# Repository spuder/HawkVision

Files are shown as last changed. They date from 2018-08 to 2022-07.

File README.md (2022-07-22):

# HawkVision

Adapter board that makes it easy to mount a TBS unify nano to the Hawk 5

[Available for purchase on etsy](https://www.etsy.com/listing/630369832/hawk-vision-vtx-realpit?ref=shop_home_active_1)



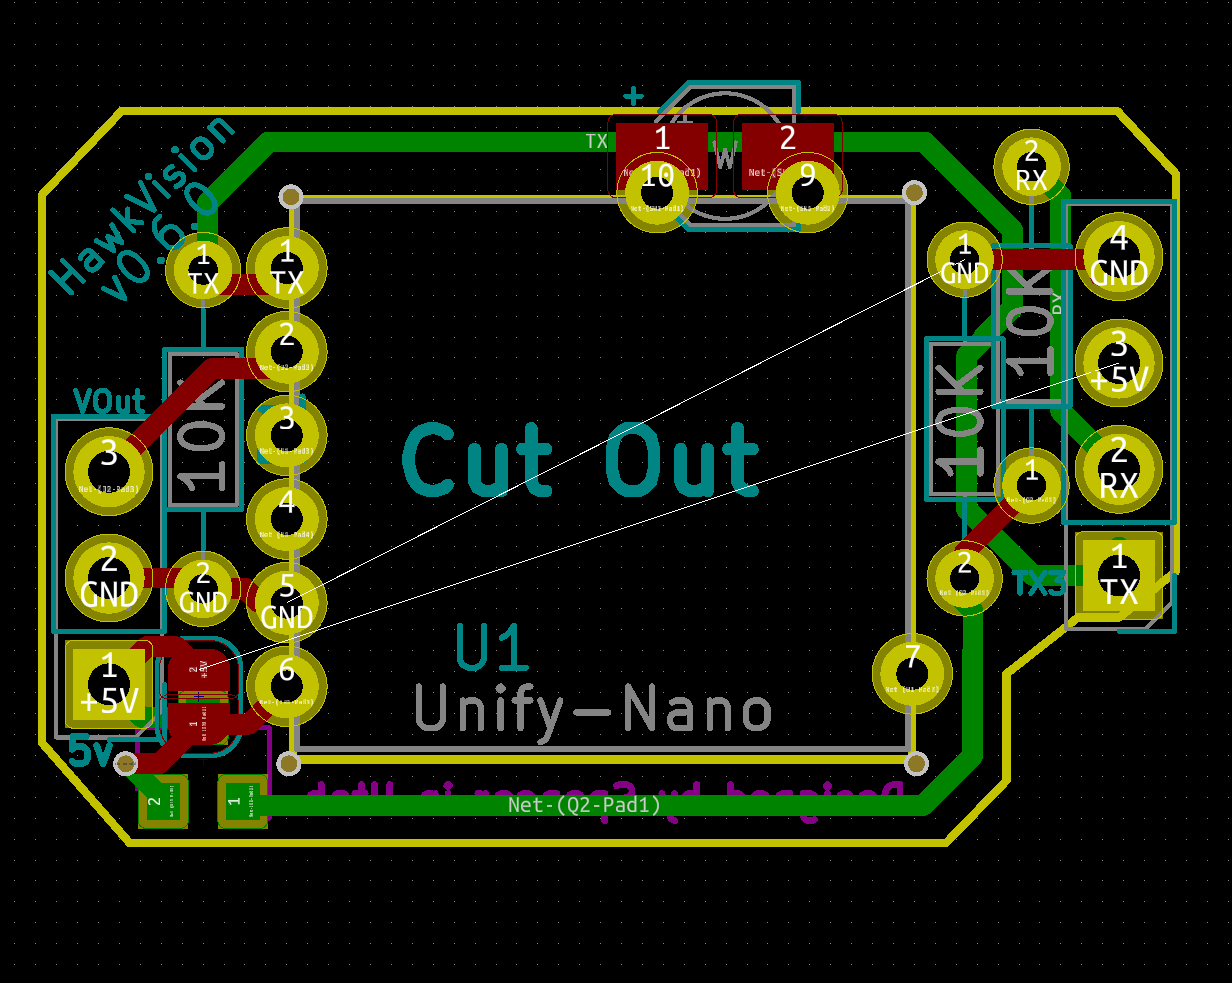
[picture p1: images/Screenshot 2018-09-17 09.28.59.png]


Based off the same idea as [whitenoise FPV](https://whitenoisefpv.com/collections/electronics/products/unify-nano-mounting-board) but designed specifically for the emax stack

## Schematic

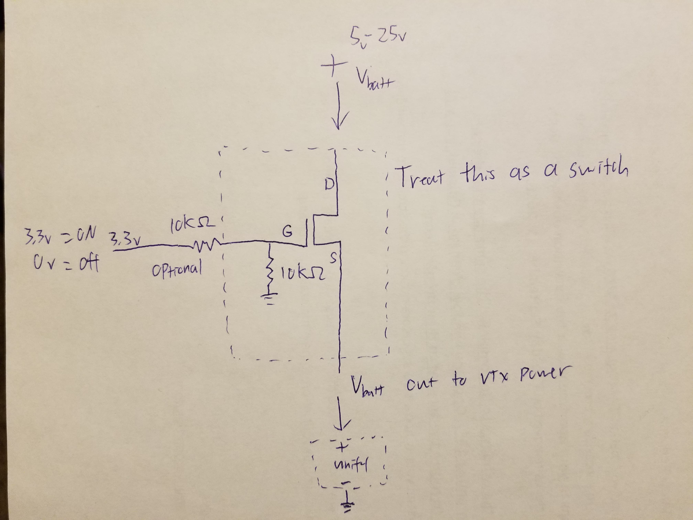
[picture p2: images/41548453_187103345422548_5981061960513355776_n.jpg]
  
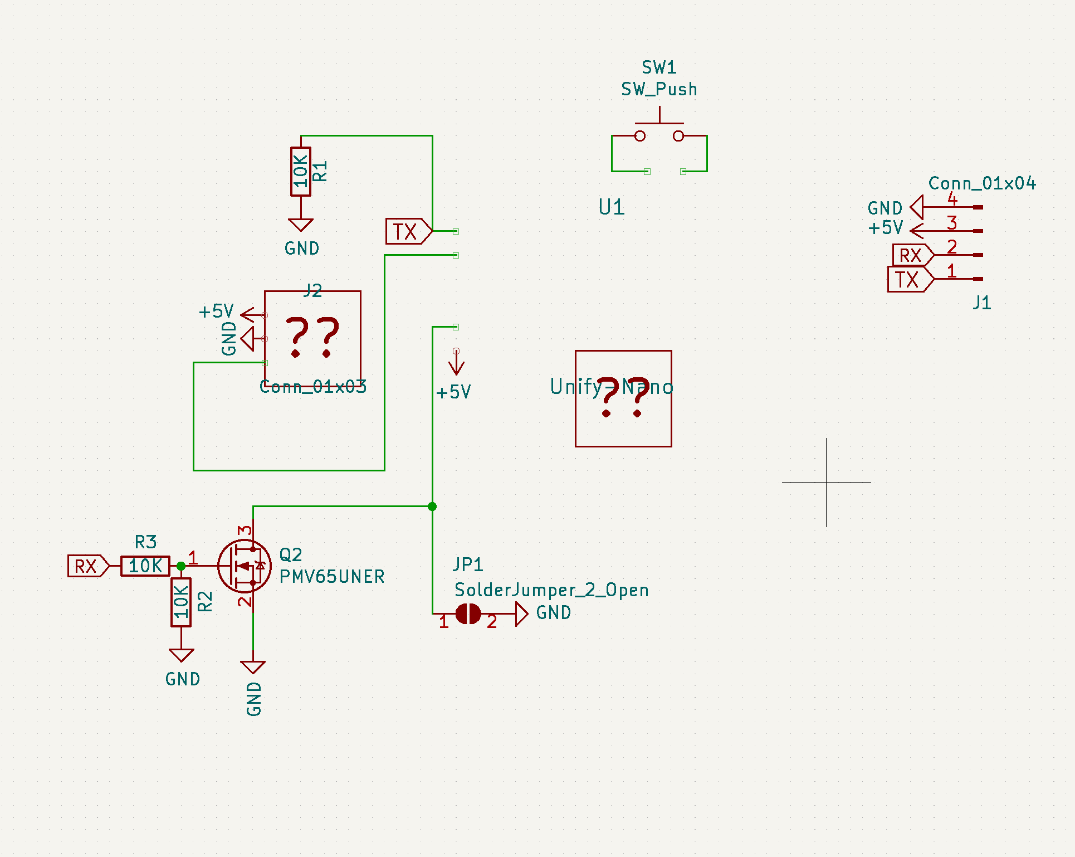
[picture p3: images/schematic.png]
  
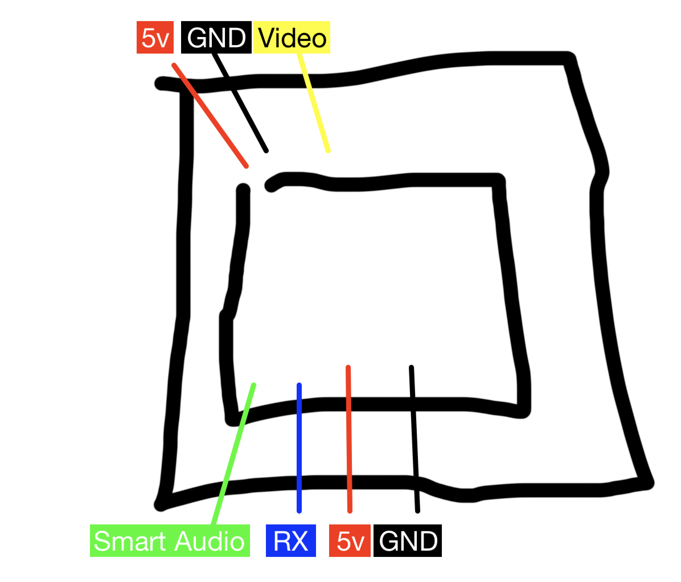
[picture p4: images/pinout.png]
  

## BOM

Any N-Channel mosfet _should_ work as log as it is a 'logic level mosfet'. A logic level mosfet has a VGS (aka gate voltage or Gate-Source threshold voltage MAX which is less than 5v or 3.3 volts). (e.g a VGS of 4.0 would work on a 5v arduino, but not a 3.3v arduino. 

- [N Channel Mosfet 863-NTR4501NT1G](https://www.mouser.com/ProductDetail/863-NTR4501NT1G)  <- Most shipped units were this model
- [N Channel Mosftet  PVM64UNE](https://www.mouser.com/ProductDetail/771-PMV65UNER) 
- [10K Resistors](https://www.mouser.com/ProductDetail/660-CFS1-4C103J)  
- [N Channel Mosfet SSM3K344R](https://www.mouser.com/ProductDetail/757-SSM3K344RLF)  
- [N Channel Mosfet 2N7000](https://www.mouser.com/ProductDetail/512-2N7000)  

Additional parts

- https://www.sparkfun.com/products/10213
- https://www.adafruit.com/product/355

### Resources

https://dronebotworkshop.com/transistors-mosfets/  
https://forum.arduino.cc/t/need-a-3-3v-logic-level-mosfet/933013/2  
https://electronics.stackexchange.com/a/235682/23954

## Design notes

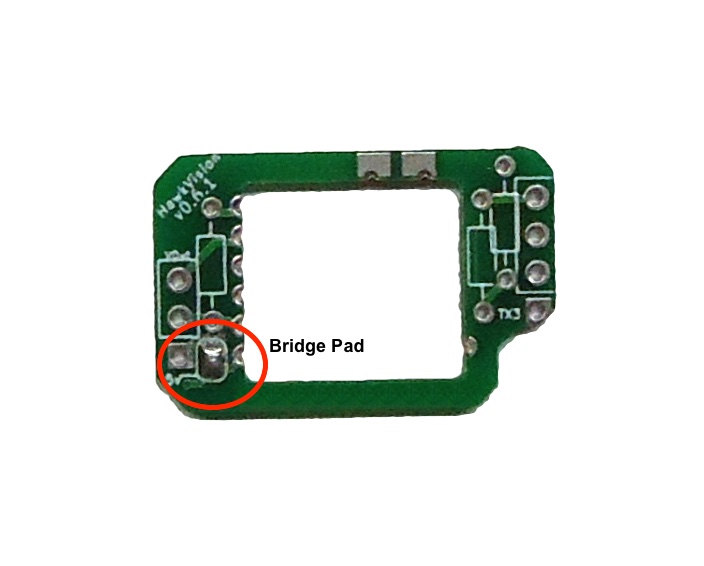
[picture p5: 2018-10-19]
images/HawkVisionBare.jpg

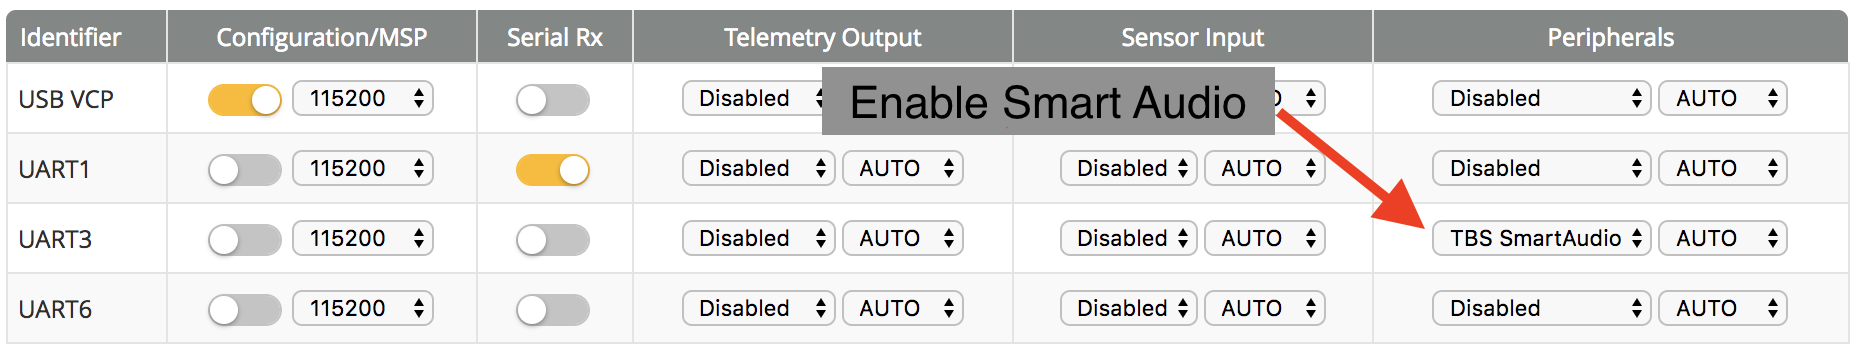
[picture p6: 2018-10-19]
images/Screenshot 2018-10-07 03.58.42.png

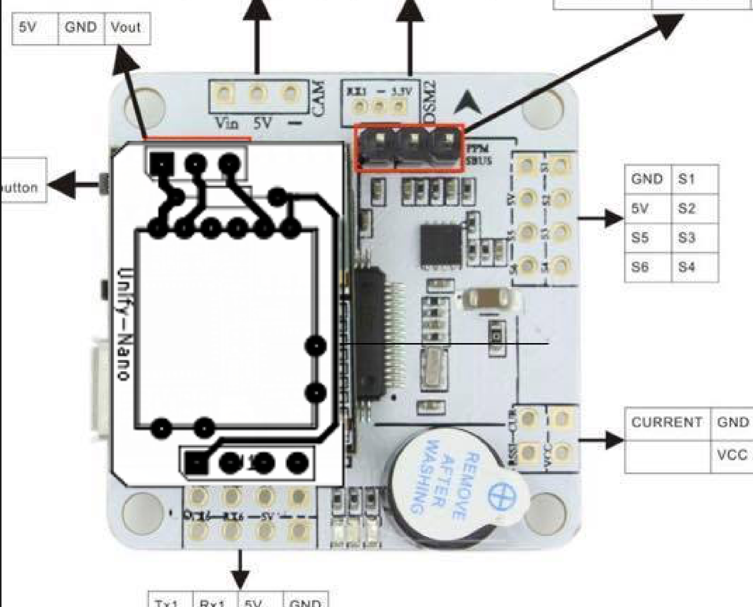
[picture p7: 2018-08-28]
images/Screenshot 2018-08-19 19.03.30.png

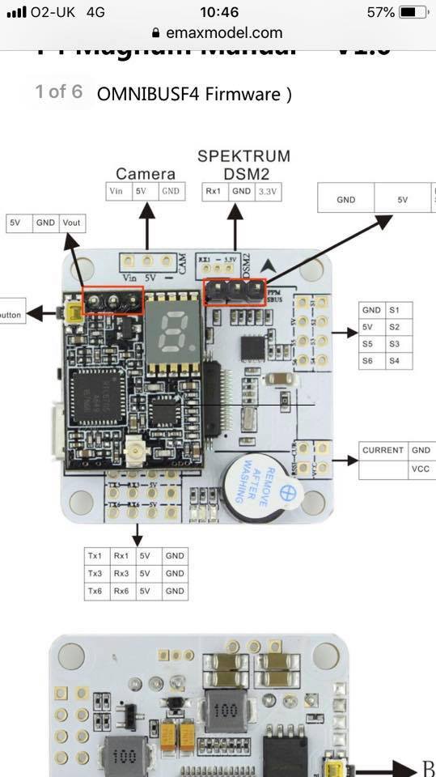
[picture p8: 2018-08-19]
images/vtx.jpg

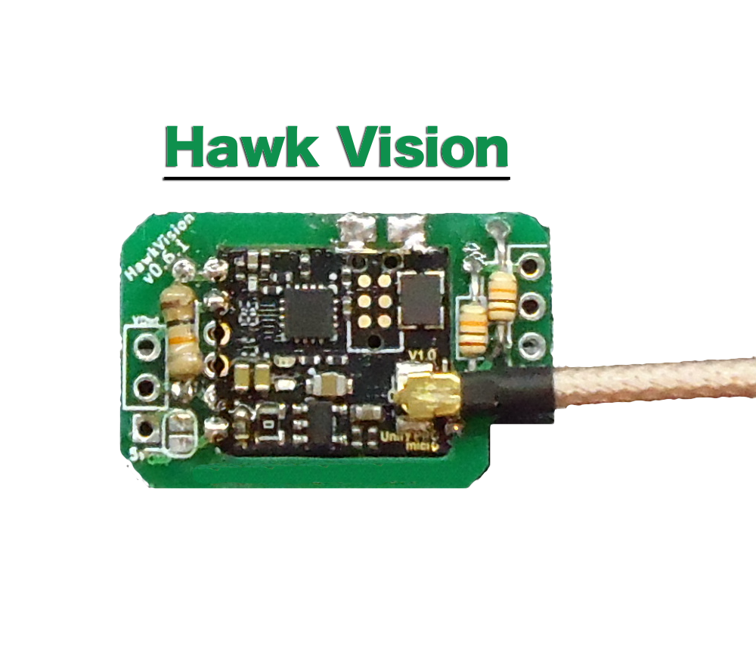
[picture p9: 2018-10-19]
images/HawkVisionRealPit.png

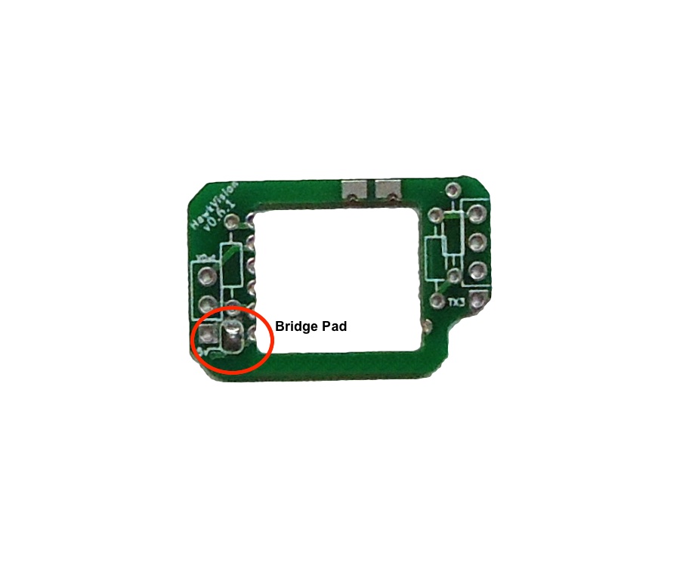
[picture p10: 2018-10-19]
images/HawkVisionBareBridge.jpg

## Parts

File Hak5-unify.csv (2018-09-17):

Id | Designator | Package | Quantity | Designation | Supplier and ref
1 | Q2 | SOT-23 | 1 | PMV65UNER
2 | R2,R3 | R_Axial_DIN0204_L3.6mm_D1.6mm_P5.08mm_Horizontal | 2 | 10K

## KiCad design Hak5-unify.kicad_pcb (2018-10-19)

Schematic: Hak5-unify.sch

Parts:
J1: Conn_01x04; Pin_Header_Straight_1x04_Pitch2.54mm
J2: Conn_01x03; Pin_Header_Straight_1x03_Pitch2.54mm
JP1: SolderJumper_2_Open; SolderJumper-2_P1.3mm_Open_RoundedPad1.0x1.5mm
Q2: PMV65UNER; SOT-23
R1, R2, R3: 10K; R_Axial_DIN0204_L3.6mm_D1.6mm_P7.62mm_Horizontal
SW1: SW_Push; CP_Elec_3x5.3
U1: Unify-Nano; unify-nano

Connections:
+5V: J1.3, J2.1, U1.6
GND: J1.4, J2.2, JP1.2 (B), Q2.2 (S), R1.2, R2.1
unnamed: J2.3, U1.2
unnamed: JP1.1 (A), Q2.3 (D), U1.5
unnamed: Q2.1 (G), R2.2, R3.1
unnamed: SW1.1, U1.10
unnamed: SW1.2, U1.9
RX: J1.2, R3.2
TX: J1.1, R1.1, U1.1

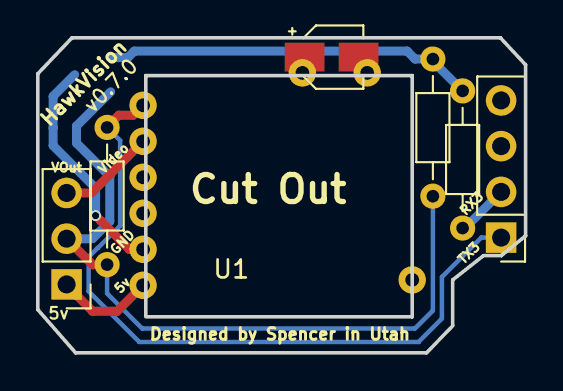
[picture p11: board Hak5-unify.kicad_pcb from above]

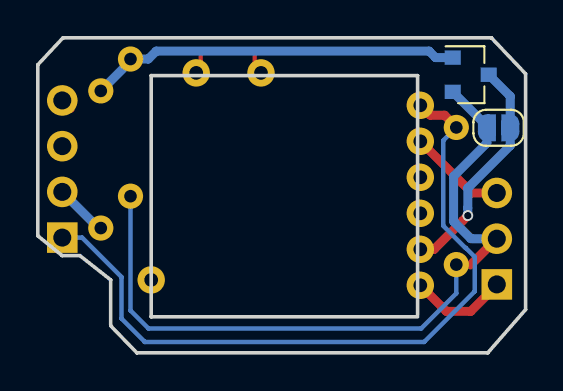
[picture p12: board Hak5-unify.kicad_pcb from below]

Board: 2 copper layers, 27.1 x 17.5 mm, 9 parts (2 on the bottom side), 9 nets.

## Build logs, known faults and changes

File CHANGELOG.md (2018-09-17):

# v0.6.0
Add solder pads for button
Use larger restistors
Remove unneeded ground pad to give more room near bottom
Move traces to underside
Add vias in the corners to improve cutout

# v0.4.1
Only do partial cutout at VTX to improve clearance for screws

# v0.4.0
Only 2 holes to hold VTX
Uses UART 3 instead of UART 1

# v0.3.0
Improved cutout for screw
Move wire to 'inside' of pads
shorten length of total board
put in initial order at jlcpcb

#v0.2.1

Improved cutout for screw
Panelization

#v0.2.0

Fix pin spacing

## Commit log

2018-08-31 designed by spencer
    [Hak5-unify-B.Cu.gbr, Hak5-unify-B.Mask.gbr, Hak5-unify-B.SilkS.gbr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]
2018-09-02 plot 0.2.1
    [Hak5-unify.kicad_pcb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]
2018-09-03 no panelization
    [Hak5-unify.kicad_pcb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]
2018-09-04 slightly different corner cutout
    [Hak5-unify-B.Cu.gbr, Hak5-unify-B.SilkS.gbr, Hak5-unify-Edge.Cuts.gbr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]
2018-09-08 fixes 2holes
    [Hak5-unify.kicad_pcb]
2022-07-21 update mosfets in readme
